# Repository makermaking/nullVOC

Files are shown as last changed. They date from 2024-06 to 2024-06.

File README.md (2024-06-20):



# (null)VOC
The carbon filter that fits in your Micron+ without mods!

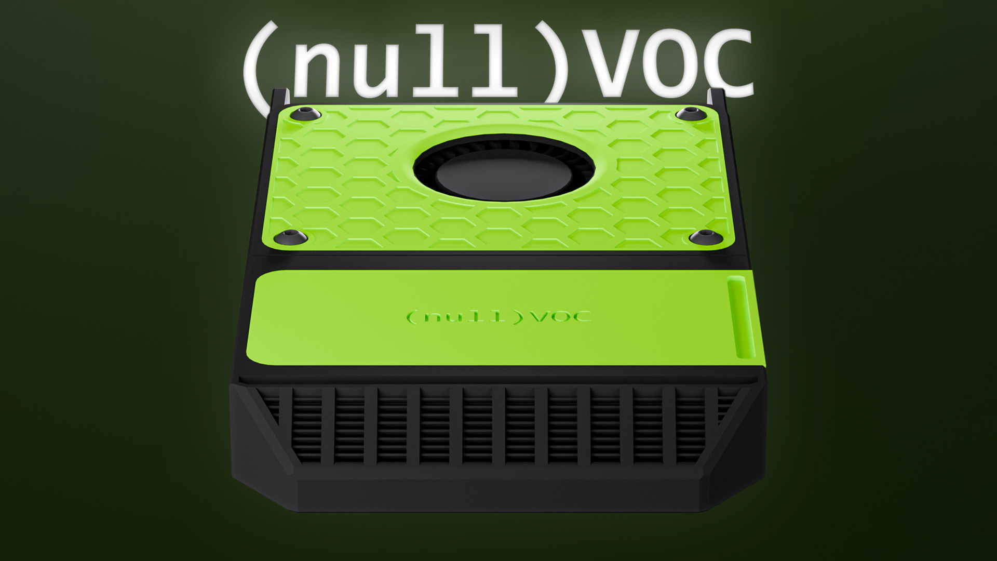
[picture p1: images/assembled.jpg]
assembled nullVOC Carbon Filter


- [(null)VOC Background](#nullVOC-background)
- [BOM](#BOM)
- [Printed Parts BOM](#Printed-Parts-BOM)
- [Printed Parts Considerations](#Printed-Parts-Considerations)
- [Assembly](#Assembly)
- [Installation](#Installation)
- [Klipper configuration](#Klipper-configuration)

## (null)VOC Background

When it came time to choose which mods I was going to use on my Micron+, I realized that the only option at the moment was 3DPF, a very good project, but in my opinion, it could have some improvements and a slightly more "Voron" aesthetic.

**(null)VOC is based on:**
- [The original Nevermore](https://github.com/nevermore3d/Nevermore_Micro) (Lots of good info on carbon filters on this page)
- [3DPF by @Jadecky](https://github.com/Jadecky/3DPF) 
- [The ZeroFilter by @zruncho](https://github.com/zruncho3d/zerofilter)

This is one of the most complex projects I have done to date, and when designing it, I did not have a clear idea from the beginning. Therefore, the design is not very parametric due to poor organization during its creation, leading to numerous fusion errors when making the slightest change. I will try to improve the base file and upload the enhanced version, but this does not affect the final design itself, just in case you want to modify it.

**Some main features of (null)VOC:**
- Designed to fit under the bed of the Micron+ without mods (3DPF does not fit in FORMBOT kits by default)
- Click-on lid
- Magnetically connected cartridge
- JST-XH connection or cable adapter
- Directed airflow
- Reduced hardware and printed parts by 50% when compared to 3DPF

## BOM
Qty |Part|Notes
---|----|---
8x|6x3 Magnets
6x|Voron Spec Brass Heatset Inserts|M3x5Dx4.5W
2x|M3x8 FHCS|M3x6 / M3x10 FHCS will also work for attaching the fan to the plenum
4x|M3x6 BHCS|M3x8 / M3x10 BHCS will also work for the plenum lid
2x|M3x6 BHCS|To mount the plenum to the extrusions
1x|5015 Blower Fan
1x|JST-XH Female|Optional

## Printed Parts BOM
Qty|STL
---|---
1x|Plenum
1x|Cartridge 
1x|Plenum Lid
1x|Cartridge Lid

## Printed Parts Considerations
- You don't need any support for any part.
- You should print the part in the default orientation of the STL.
- You must print the parts in ABS if you dont want to burn all pieces.

## Assembly
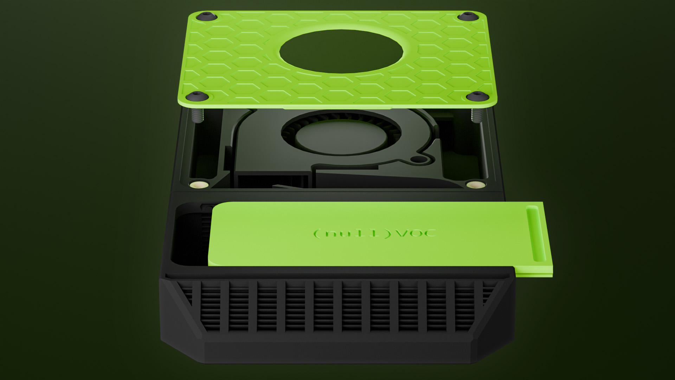
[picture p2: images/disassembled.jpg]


- Glue the 8x magnets into the plenum and the cartridge\
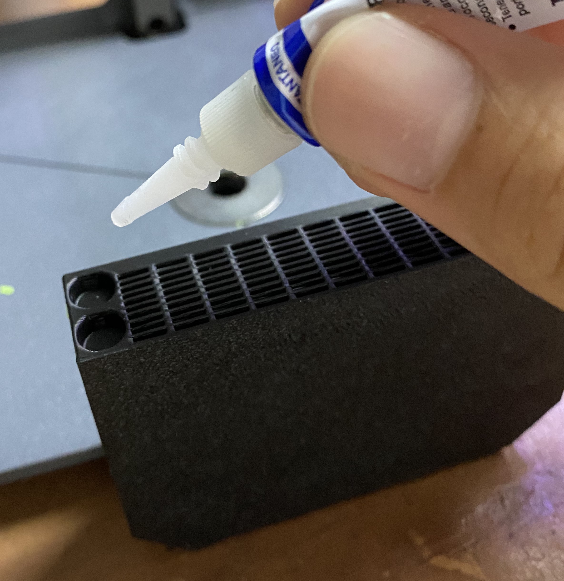
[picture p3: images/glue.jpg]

**ATTENTION!**\
Make sure that before gluing the magnets, the poles of the magnets on the cartridge and the plenum match with each other, speaking from experience :(
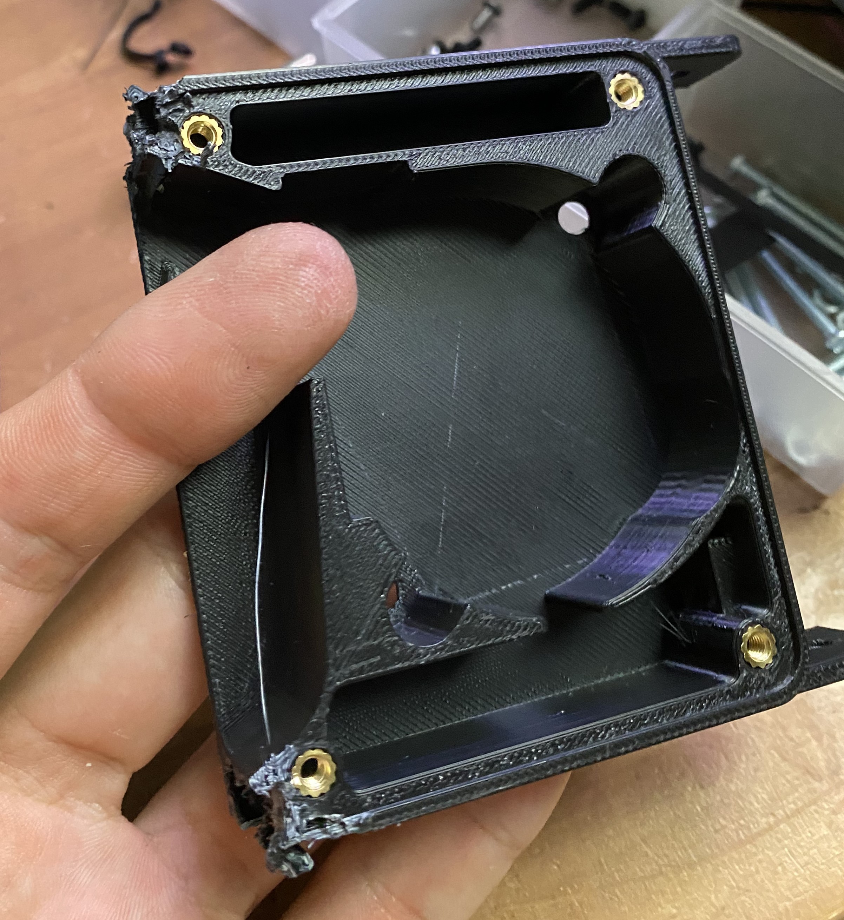
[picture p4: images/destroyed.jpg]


- Insert 4x heatsets into the Plenum for the lid securing screws.
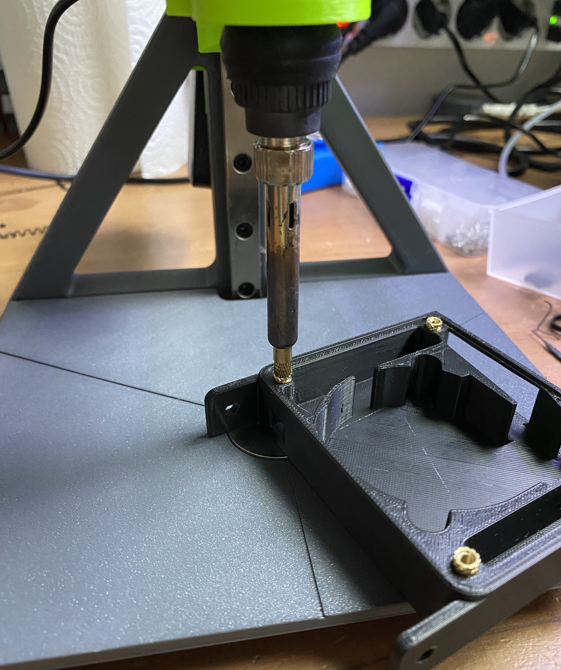
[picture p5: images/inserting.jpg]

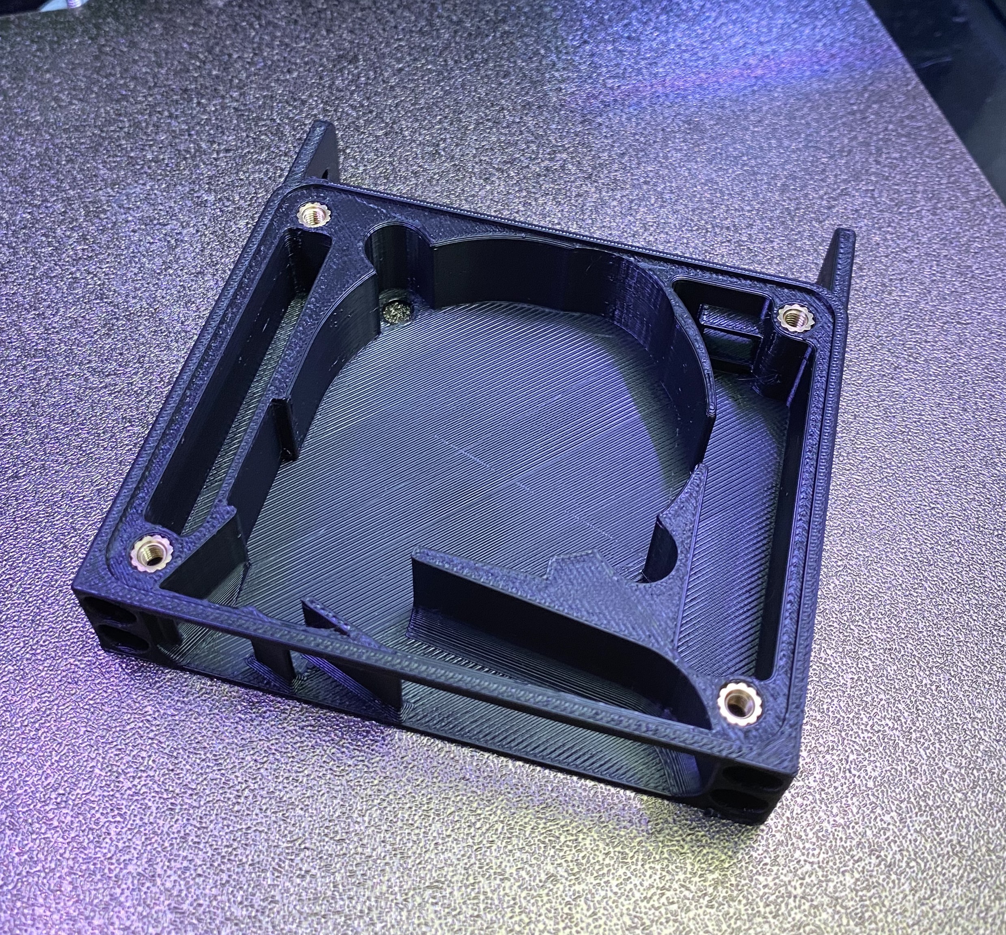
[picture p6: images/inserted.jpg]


- Insert 2x heatsets into the bottom of the screw tabs on the 5015 fan.
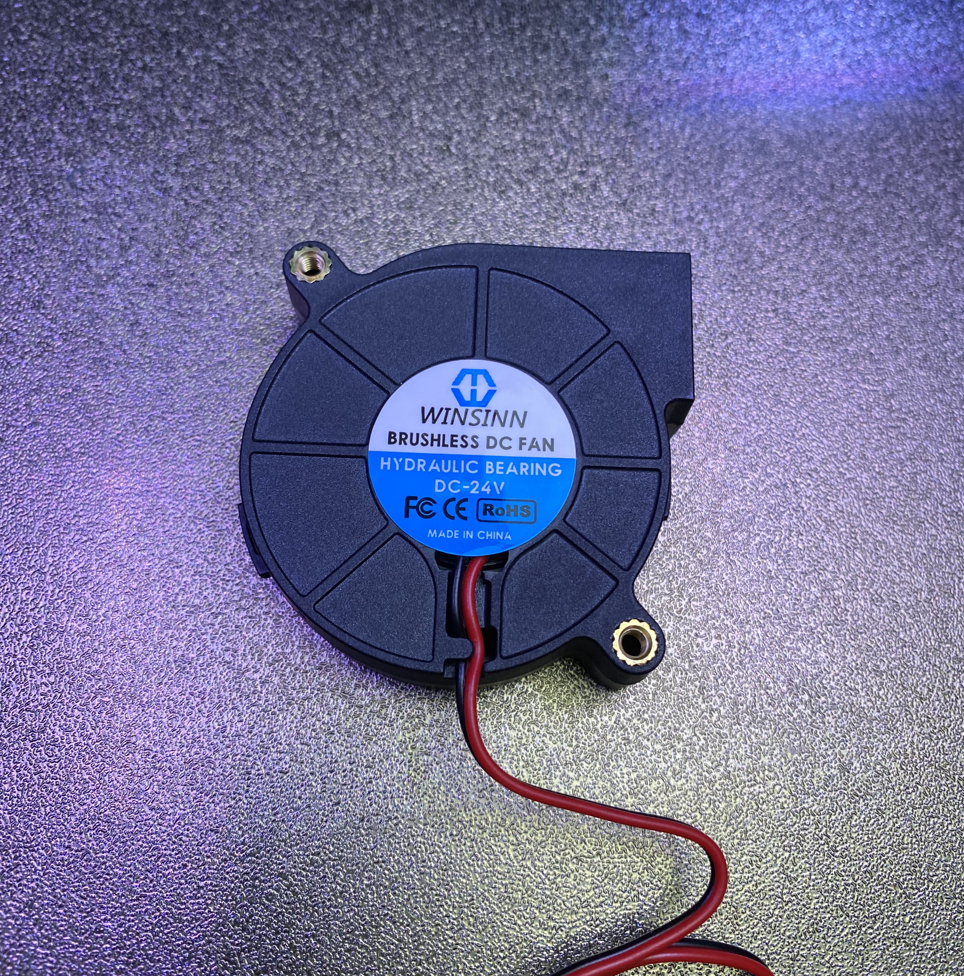
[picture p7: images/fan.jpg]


- You may need to recess them 1-2 mm to allow the screws to sit correctly on the underside of the plenum.
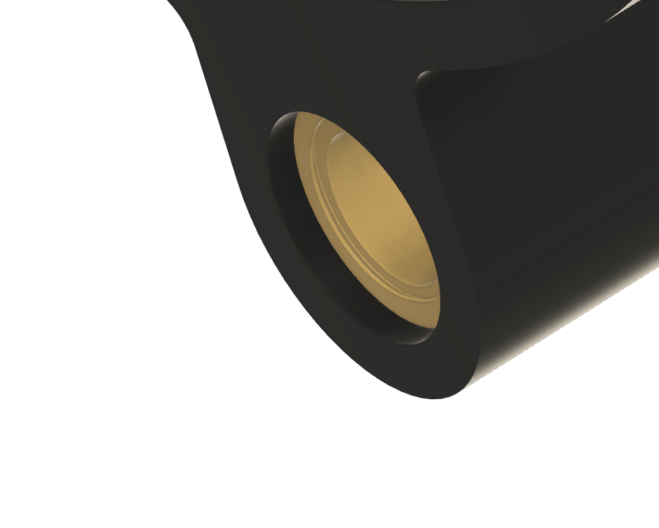
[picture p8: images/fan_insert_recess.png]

_(Photo from 3DPF)_

- Screw 2x M3x8 BHCS on the bottom of the plenum to attach the fan.
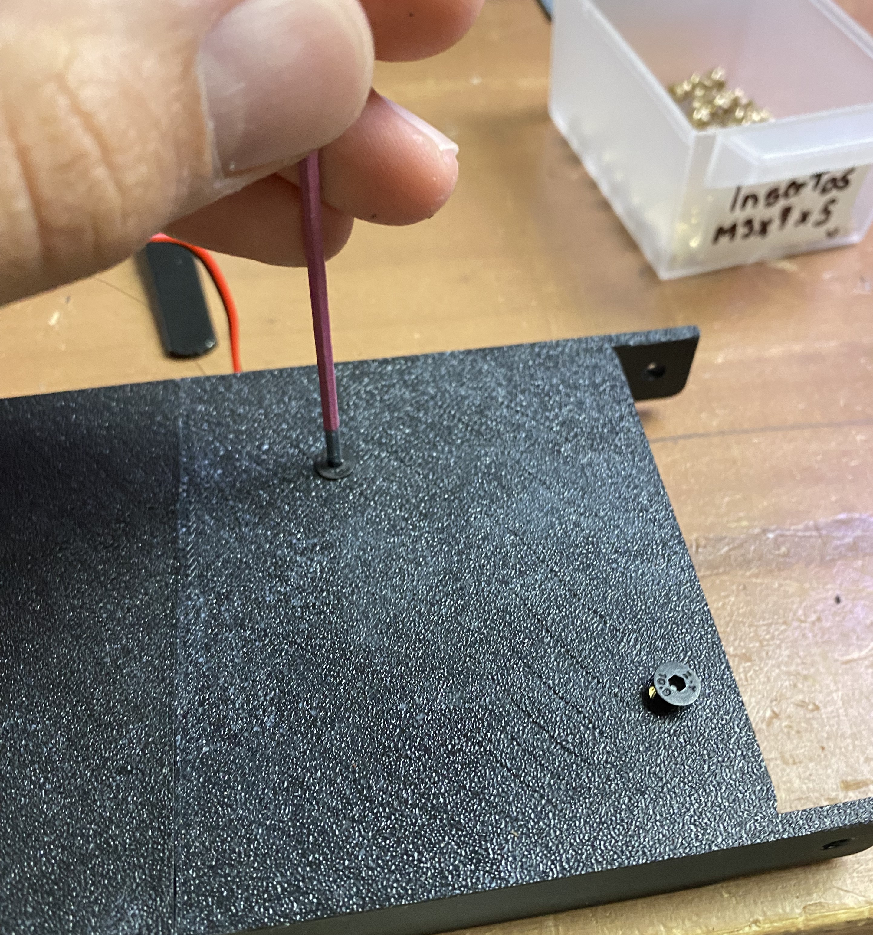
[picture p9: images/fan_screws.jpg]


**If you simply want to run the fan cable directly, ignore the following two steps and print [this file](https://github.com/makermaking/nullVOC/blob/f42df72e84823ff277ccc7cc3c3beba2df1983ff/beta1/STLs/Dummy%20cover%20(optional).stl), which will allow you to insert the cable and then fit it into the same hole where the JST connector goes.**

- Solder the two fan wires to the JST-XH connector, paying attention to the polarity (Included an image for reference).
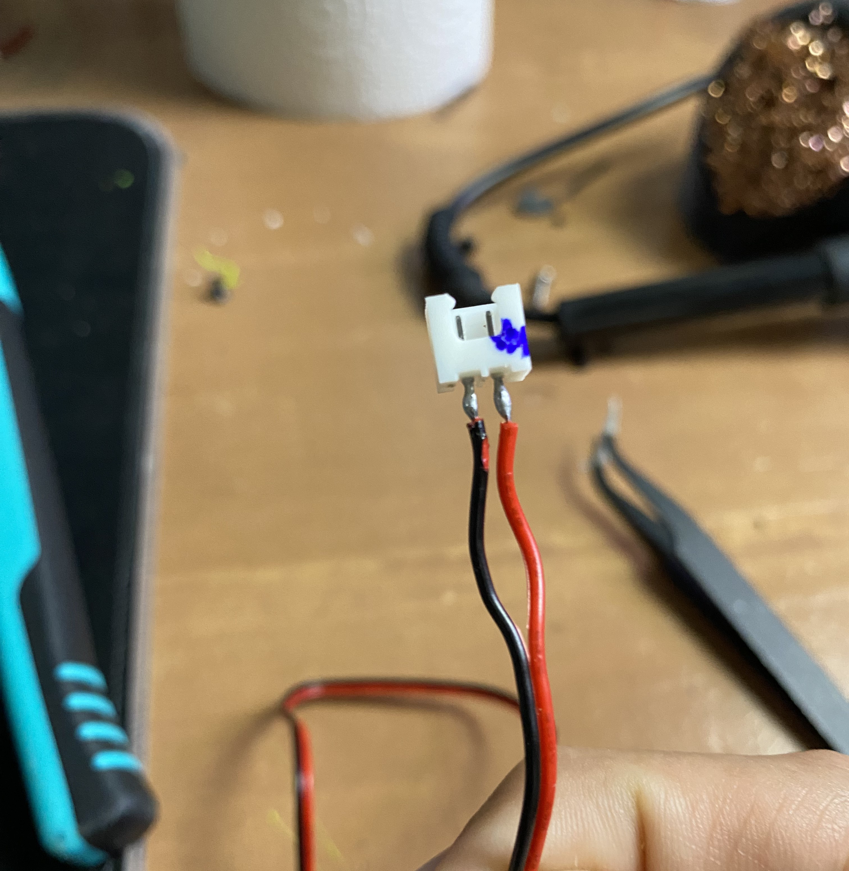
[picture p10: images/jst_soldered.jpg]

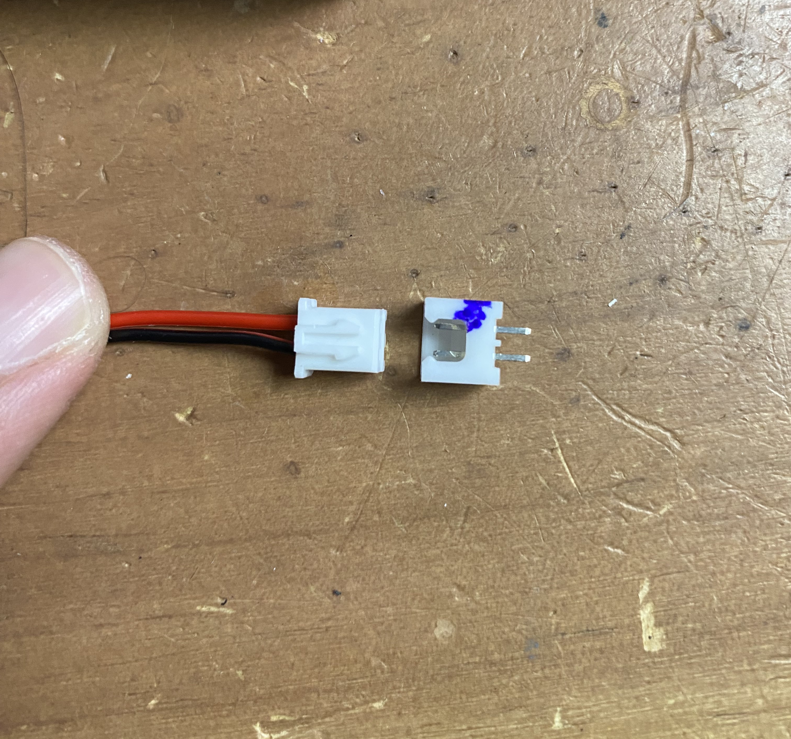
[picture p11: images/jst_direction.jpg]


- With the connector soldered, insert it into the hole where it should fit tightly (make sure to push it all the way in). Spread hot silicone to keep the connector and its connections in place. You can leave the excess cable in the hole (as shown in the image) or you can cut it directly.
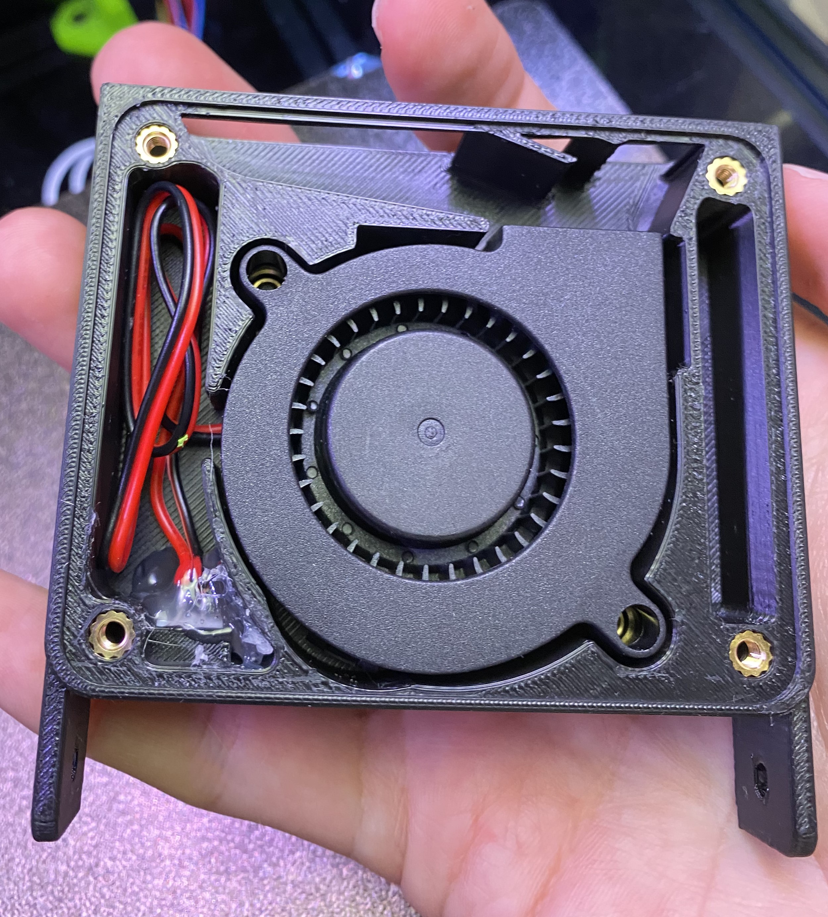
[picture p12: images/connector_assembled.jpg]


_The hard part is done!_

- Insert the leading edge of the plenum lid into the small gap, and then press the lid down until it is fully inserted.
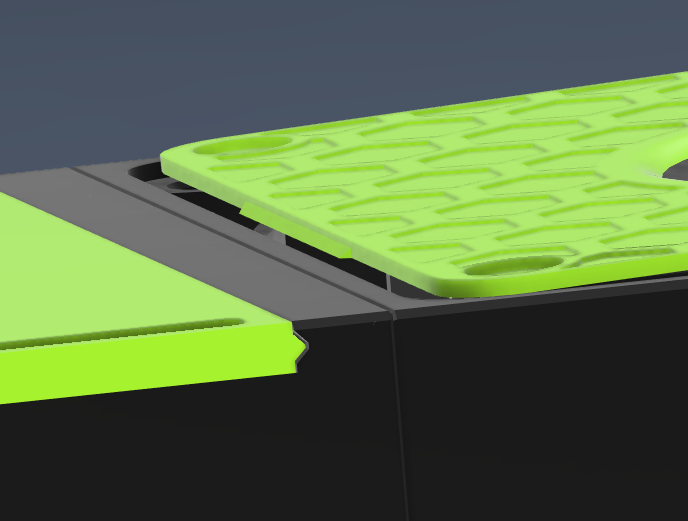
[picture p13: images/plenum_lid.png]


- Screw 4x M3x6 BHCS to secure the lid into the plenum.

- Slide in the lid into the cartridge.\


Congrats! Now it is fully assembled, let's install it!

## Installation
- First, you will need to remove the bed.
- With the bed removed, you can insert one nut into each bed extrusion.
- Now you can pass the cable through the hole and screw in a screw on each side to its respective nut. It's normal for the fins to flex a bit due to the tolerance that may exist between the two extrusions, but don't worry because the flexion is minimal.
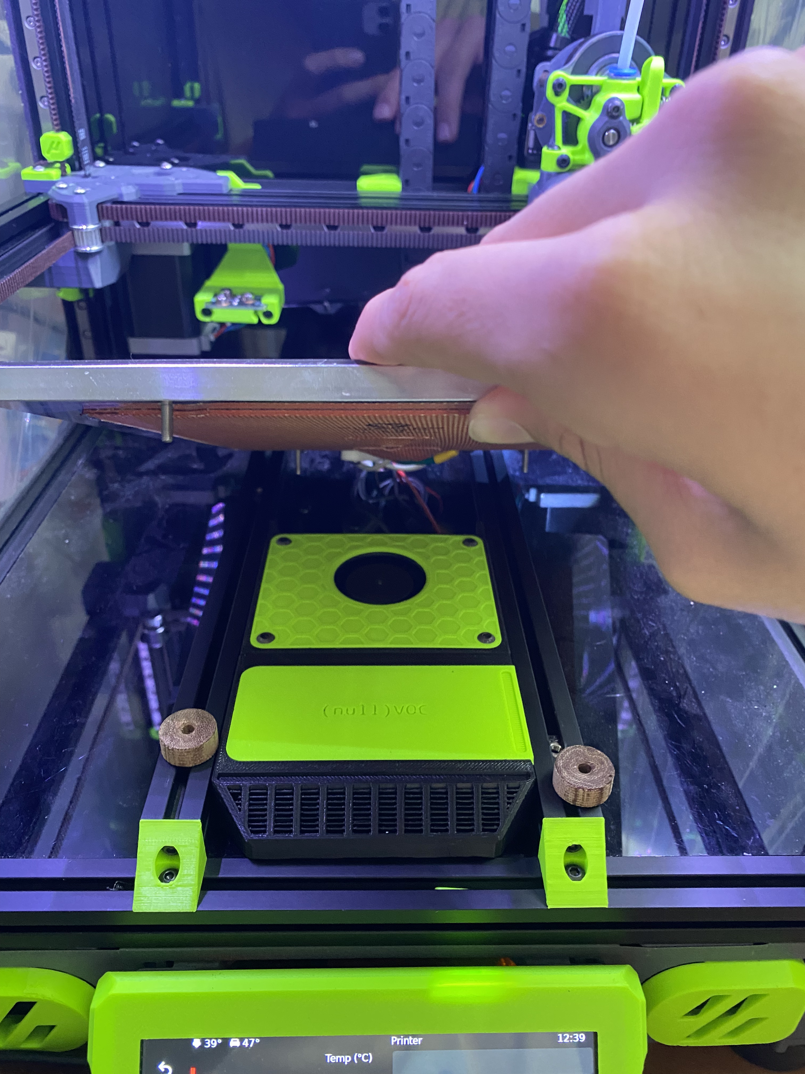
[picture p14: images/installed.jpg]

- Search "Your motherboard + pinout" on Google and you'll be able to find out which ports are available for connecting fans.

## Klipper configuration
My configuration sets that when the bed reaches 90°C, the fan will turn on and will turn off as soon as the target temperature is below 90°C. This way, when printing with ABS, which in my setup requires a bed temperature of 105°C, the fan will turn on.
```
[heater_fan nullvoc]
pin: YOUR FAN PIN
heater: heater_bed
heater_temp: 90.0
fan_speed: 1
```

##(null)VOC still in BETA
If you have any problem, suggestion or question, you can contact me at the user-projects section of [DOOMCUBE Discord](https://discord.gg/doomcube)

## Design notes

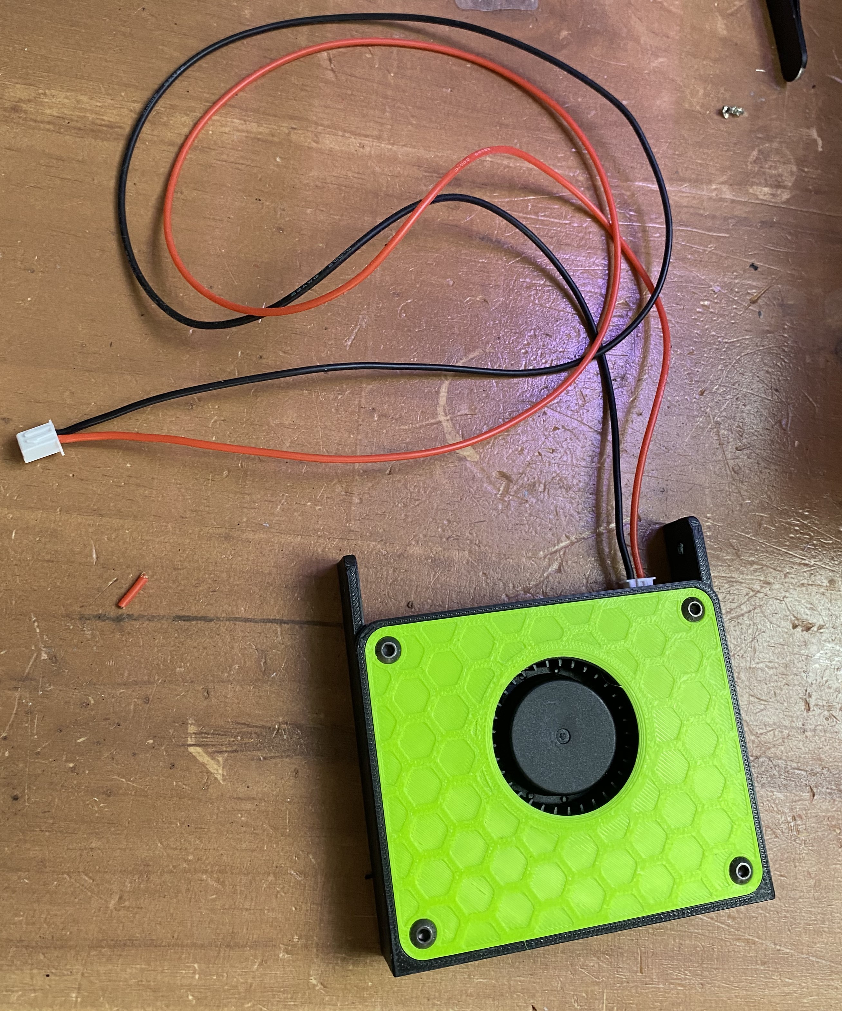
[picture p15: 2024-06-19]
images/connected.jpg

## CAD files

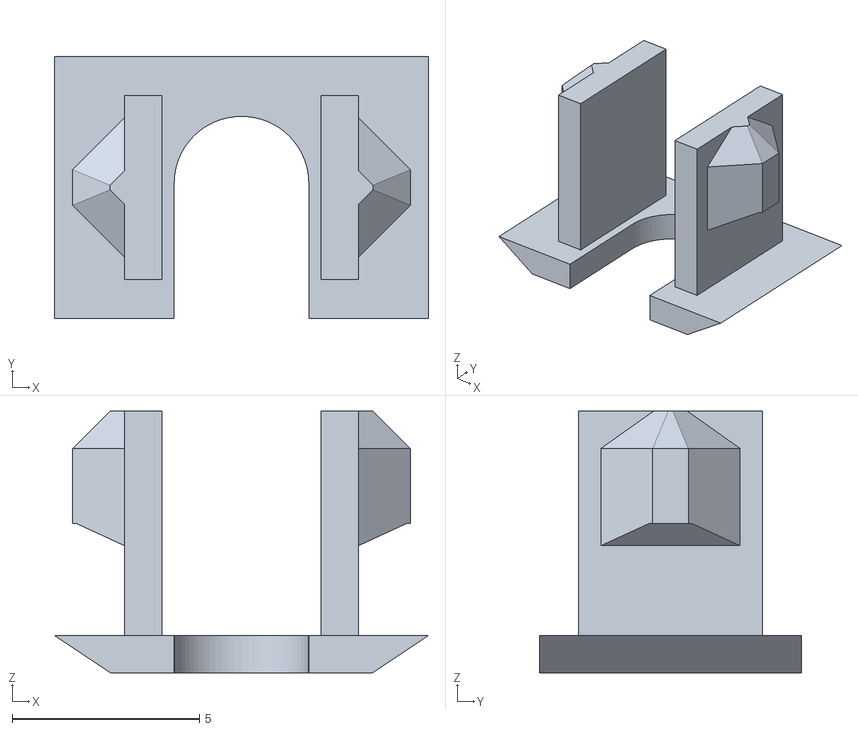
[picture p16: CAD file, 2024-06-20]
beta1/STLs/Dummy cover (optional).stl
10.00 x 7.00 x 7.00

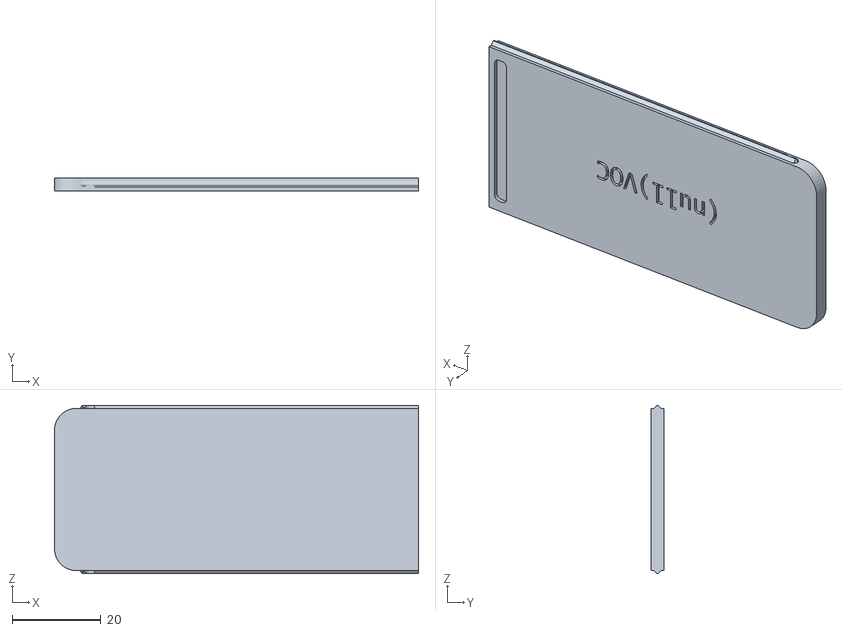
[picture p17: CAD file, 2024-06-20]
beta1/STLs/Lid.stl
81.9 x 3.00 x 37.9

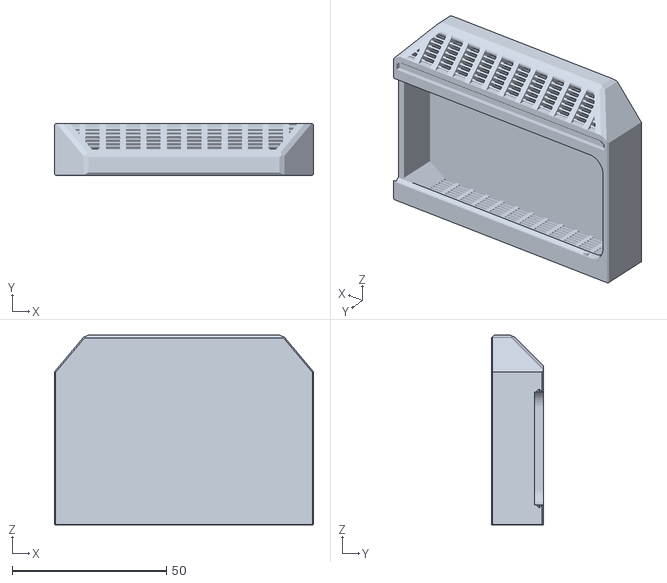
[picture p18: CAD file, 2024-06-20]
beta1/STLs/Cardtridge.stl
84.0 x 17.0 x 61.6

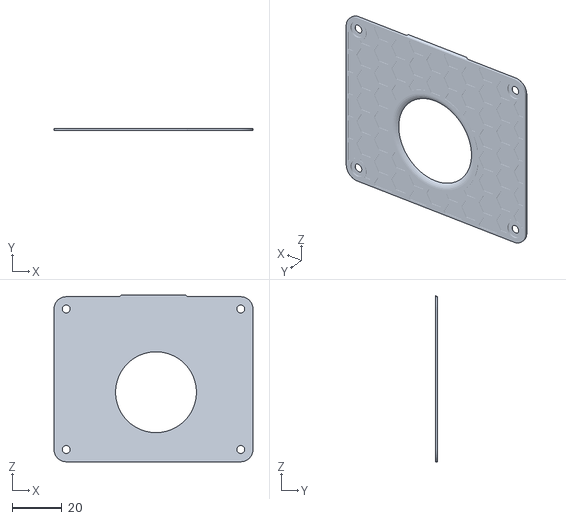
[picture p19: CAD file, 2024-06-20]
beta1/STLs/PlenumLid.stl
79.8 x 1.00 x 66.8

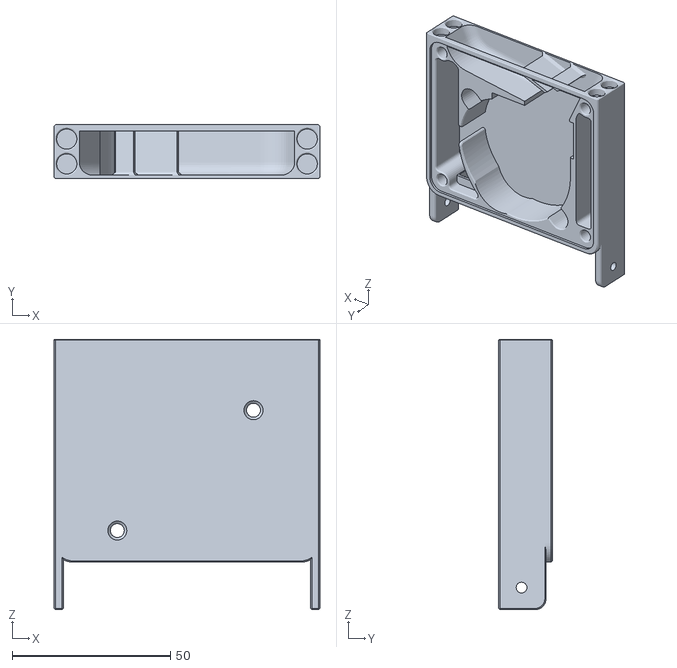
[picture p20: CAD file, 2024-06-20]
beta1/STLs/Plenum.stl
84.0 x 17.0 x 85.4
